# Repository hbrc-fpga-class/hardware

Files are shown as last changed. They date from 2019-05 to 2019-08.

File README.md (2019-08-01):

# Homebrew Automation Hardware

This repository contains the designs for any physical hardware for the Homebrew Automation PCB.

# tinyfpga-raspi-romi-board
These are the KiCad design files for the PCB. It's designed as follows:

* The Romi chassis needs to have the combined power distribution board and motor controller
* The Romi PDB/MC's onboard regulator **NEEDS TO BE CONFIGURED TO 3.3V OUTPUT OR EVERYTHING WILL BREAK AND YOU WILL BE SAD**
  * This is accomplished by cutting the "VREG Select" trace with an exacto knife. 
* Male headers need to be installed into the following locations (add a picture here....)
  * PWMR / DIRR / nSLPR / GND
  * PWML / DIRL / nSLPL / GND
  * ERA / ERB / GND
  * ELA / ELB / GND
  * 3x VSW / 3x GND
* The custom board should have female headers installed which mate with the male headers on the PDB/MC board
* The raspberry pi and tinyfpga plug into the custom board

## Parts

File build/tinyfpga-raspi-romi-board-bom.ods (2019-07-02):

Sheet: tinyfpga-raspi-romi-board
17 | R11, R12, R13, R14, R15, R16, R17, R18, R19, R20, R21, R3, R4, R5, R6, R7, R8 | 268 | Resistor_THT:R_Axial_DIN0204_L3.6mm_D1.6mm_P2.54mm_Vertical
1 | F1 | MF-MSMF250/16X-2 | Fuse:Fuse_1812_4532Metric_Pad1.30x3.40mm_HandSolder
1 | C2 | 1uF | Capacitor_THT:C_Rect_L4.0mm_W2.5mm_P2.50mm
1 | C1 | 22uF | Capacitor_THT:CP_Radial_D5.0mm_P2.00mm
8 | Q1, Q2, Q3, Q4, Q5, Q6, Q7, Q8 | 2N7000 | Package_TO_SOT_THT:TO-92_Inline
10 | R1, R10, R2, R22, R23, R24, R25, R26, R27, R9 | 3.9k | Resistor_THT:R_Axial_DIN0204_L3.6mm_D1.6mm_P2.54mm_Vertical
1 | U1 | CAT24C128 | Package_SO:SOIC-8_3.9x4.9mm_P1.27mm
2 | J1, J2 | PinSocket_1x14_P2.54mm_Vertical | Connector_PinSocket_2.54mm:PinSocket_1x14_P2.54mm_Vertical
8 | D2, D3, D4, D5, D6, D7, D8, D9 | LED | LED_THT:LED_D5.0mm_Clear
1 | A1 | OKR-T_3-W12-C | custom:Murata_OKR-T-3_P73
3 | J19, J6, J8 | PinHeader_1x02_P2.54mm_Vertical | Connector_PinHeader_2.54mm:PinHeader_1x02_P2.54mm_Vertical
2 | J16, J17 | PinHeader_1x03_P2.54mm_Vertical | Connector_PinHeader_2.54mm:PinHeader_1x03_P2.54mm_Vertical
1 | J9 | PinHeader_1x06_P2.54mm_Vertical | Connector_PinHeader_2.54mm:PinHeader_1x06_P2.54mm_Vertical
1 | J20 | PinHeader_2x05_P2.54mm_Vertical | Connector_PinHeader_2.54mm:PinHeader_2x05_P2.54mm_Vertical
1 | J7 | PinHeader_2x08_P2.54mm_Vertical | Connector_PinHeader_2.54mm:PinHeader_2x08_P2.54mm_Vertical
2 | J10, J11 | PinSocket_1x03_P2.54mm_Vertical | Connector_PinSocket_2.54mm:PinSocket_1x03_P2.54mm_Vertical
2 | J14, J15 | PinSocket_1x04_P2.54mm_Vertical | Connector_PinSocket_2.54mm:PinSocket_1x04_P2.54mm_Vertical
2 | J12, J13 | PinSocket_2x02_P2.54mm_Vertical | Connector_PinSocket_2.54mm:PinSocket_2x02_P2.54mm_Vertical
1 | J5 | PinSocket_2x03_P2.54mm_Vertical | Connector_PinSocket_2.54mm:PinSocket_2x03_P2.54mm_Vertical
1 | J4 | PinSocket_2x08_P2.54mm_Vertical | Connector_PinSocket_2.54mm:PinSocket_2x08_P2.54mm_Vertical
1 | J3 | PinSocket_2x20_P2.54mm_Horizontal | Connector_PinSocket_2.54mm:PinSocket_2x20_P2.54mm_Horizontal
1 | D1 | SMBJ5.0A | Diode_SMD:D_SMB_Handsoldering
3 | SW2, SW3, SW4 | SW_Push | Button_Switch_THT:SW_PUSH_6mm_H5mm

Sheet: tinyfpga
1 | https://www.digikey.com/product-detail/en/sullins-connector-solutions/GEC03DABN-M30/S2331E-03-ND/1242106
2 | https://www.digikey.com/product-detail/en/sullins-connector-solutions/PEC14SFAN/S1212E-14-ND/859455

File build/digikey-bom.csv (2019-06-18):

Index | Quantity | Part Number | Manufacturer Part Number | Description | Customer Reference | Available | Backorder | Unit Price | Extended Price USD
1 | 25 | 811-2115-5-ND | OKR-T/3-W12-C | DC DC CONVERTER 0.59-6V 15W |  | 25 | 0 | 6.01000 | 150.25
2 | 25 | 732-8938-1-ND | 860020572004 | CAP ALUM 22UF 20% 35V RADIAL |  | 25 | 0 | 0.11000 | 2.75
3 | 25 | 445-173261-1-ND | FG18X7R1E105KRT06 | CAP CER 1UF 25V X7R RADIAL |  | 25 | 0 | 0.23700 | 5.93
4 | 25 | SMBJ5.0ALFCT-ND | SMBJ5.0A | TVS DIODE 5V 9.2V DO214AA |  | 25 | 0 | 0.27560 | 6.89
5 | 200 | C5SMF-RJF-CT0W0BB2CT-ND | C5SMF-RJF-CT0W0BB2 | LED RED CLEAR 5MM OVAL T/H |  | 200 | 0 | 0.12160 | 24.32
6 | 25 | MF-MSMF250/16X-2CT-ND | MF-MSMF250/16X-2 | PTC RESET FUSE 16V 2.5A 1812 |  | 25 | 0 | 0.71900 | 17.98
7 | 200 | 2N7000FS-ND | 2N7000 | MOSFET N-CH 60V 200MA TO-92 |  | 200 | 0 | 0.24990 | 49.98
8 | 250 | BC4555CT-ND | MRS16000C3901FCT00 | RES 3.9K OHM 1% 0.4W AXIAL |  | 250 | 0 | 0.05916 | 14.79
9 | 500 | BC4552CT-ND | MRS16000C2700FCT00 | RES 270 OHM 1% 0.4W AXIAL |  | 500 | 0 | 0.04662 | 23.31
10 | 25 | CAT24C128WI-GT3CT-ND | CAT24C128WI-GT3 | IC EEPROM 128K I2C 1MHZ 8SOIC |  | 25 | 0 | 0.30900 | 7.73
11 | 75 | 450-1650-ND | 1825910-6 | SWITCH TACTILE SPST-NO 0.05A 24V |  | 75 | 0 | 0.09400 | 7.05
12 | 25 | S5534-ND | PPTC202LJBN-RC | CONN HDR 40POS 0.1 TIN PCB R/A |  | 25 | 0 | 2.32600 | 58.15
13 | 50 | S7012-ND | PPTC141LFBN-RC | CONN HDR 14POS 0.1 TIN PCB |  | 50 | 0 | 0.80300 | 40.15
14 | 25 | S1012EC-30-ND | PREC030SAAN-RC | CONN HEADER VERT 30POS 2.54MM |  | 0 | 25 | 0.48120 | 12.03
15 | 50 | S7002-ND | PPTC041LFBN-RC | CONN HDR 4POS 0.1 TIN PCB |  | 50 | 0 | 0.42400 | 21.20
16 | 50 | S7036-ND | PPPC031LFBN-RC | CONN HDR 3POS 0.1 GOLD PCB |  | 50 | 0 | 0.35100 | 17.55
17 | 50 | S7070-ND | PPTC022LFBN-RC | CONN HDR 4POS 0.1 TIN PCB |  | 50 | 0 | 0.53500 | 26.75
18 | 25 | S5673-ND | NPTC032KFMS-RC | CONN HDR 6POS 0.1 TIN SMD |  | 25 | 0 | 0.84200 | 21.05
19 | 25 | 609-5602-ND | 54202-G08-03 | CONN HEADER SMD 6POS 2.54MM |  | 25 | 0 | 0.34200 | 8.55
20 | 25 | 609-4723-ND | 54202-G0805LF | CONN HEADER SMD 10POS 2.54MM |  | 25 | 0 | 0.67300 | 16.83
21 | 25 | 609-4723-ND | 54202-G0805LF | CONN HEADER SMD 10POS 2.54MM |  | 25 | 0 | 0.67300 | 16.83
22 | 25 | S5678-ND | NPTC082KFMS-RC | CONN HDR 16POS 0.1 TIN SMD |  | 25 | 0 | 1.71100 | 42.78
23 | 6 | S1033E-06-ND | GBC06SABN-M30 | CONN HEADER SMD 6POS 2.54MM |  | 6 | 0 | 0.84000 | 5.04

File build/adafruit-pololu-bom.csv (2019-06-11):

Qty. | Item Name | URL | Unit Price | Extended Price | Notes
1 | Raspberry Pi 3 Model B+ | https://www.adafruit.com/product/3775 | $35.00 | $35.00
1 | 8 GB SDHC MicroSD Card | https://www.adafruit.com/product/1294 | $9.95 | $9.95 | Could probably get by with 4GB card if available
2 | Alkaline AA batteries (LR6) - 3 pack | https://www.adafruit.com/product/3521 | $2.25 | $4.50 | Six batteries needed per base
1 | Male/Male Jumper Wires – 20 x 3" (75mm) | https://www.adafruit.com/product/1956 | $1.95 | $1.95 | Not all 20 are needed but they’re handy to keep around
1 | TinyFPGA BX | https://www.adafruit.com/product/4038 | $38.95 | $38.95
2 | HC-SR04 Ultrasonic Sonar Distance Sensor | https://www.adafruit.com/product/3942 | $3.95 | $7.90 | Wayne can likely supply these. Should they be sourced anyway just in case?
1 | Romi Chassis Kit - Blue | https://www.pololu.com/product/3506 | $29.95 | $29.95 | Color isn’t important. Substitute others at your own discretion
1 | Romi Encoder Pair Kit, 12 CPR, 3.5-18V | https://www.pololu.com/product/3542 | $8.95 | $8.95
1 | Motor Driver and Power Distribution Board for Romi Chassis | https://www.pololu.com/product/3543 | $19.95 | $19.95
2 | QTR-MD-01RC Reflectance Sensor | https://www.pololu.com/product/4141 | $1.61 | $3.22
 |  |  | Total: | $160.32

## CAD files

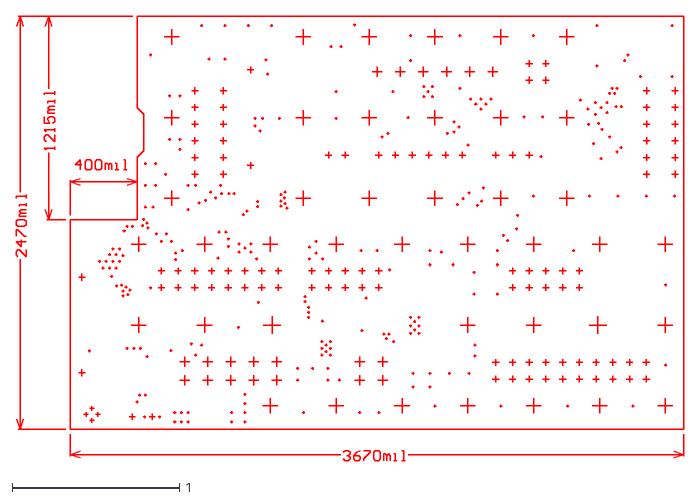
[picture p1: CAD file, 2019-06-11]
research/mech/rom02a-drill.dxf
3.99 x 2.66

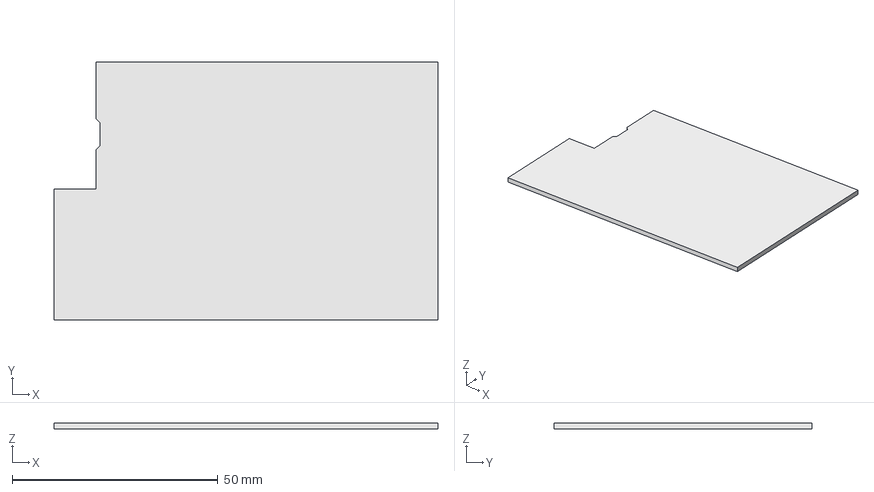
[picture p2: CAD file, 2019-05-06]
research/mech/pololu-motor-power-board.FCStd
93.2 x 62.7 x 1.57 mm

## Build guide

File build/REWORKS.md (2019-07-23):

# Homebrew Automation Board Rev A Reworks

* U1 silk is hard to understand. Doesn't _clearly_ indicate pin 1 / orientation.
* U1 address pins should probably get some thermal relief to make soldering easier
* I don't like the copper neck under F1. Looks like it could cause a short.
* While pin 1 is defined on board silk for A1, the A1 module doesn't indicate pin 1 very obviously or at all.
* I don't like the closeness of the pads for A1. Makes soldering pretty tricky when trying to avoid shorts.
* Silk on 3.3V power select is switched.
* Transistor pitch is very difficult to solder. To be honest, SOT23 would probably be easier
* Pull-downs on PWM signals are missing
* TX and RX is switched
* The male 1x14 pins I bought are too long and needed to be trimmed.
* ~Pull-down needed on romi shutdown pin~ Cut trace on shutdown pin to disable feature
* Real-time clock for Raspberry Pi
* EEPROM should always be powered from Raspberry Pi 3.3V
* In order to prevent undervolting the Pi, consider changing the 5V regulator's TRIM resistor to 255 ohm (1%)
* Add more bulk capacitance to prevent high internal resistance of Alkaline batteries from allowing VBAT

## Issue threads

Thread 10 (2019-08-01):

Silkscreen labels wrong for 3.3V power selection

swedishhat, 2019-08-01:
silk labels are switched for the headers that select the source of the 3.3V

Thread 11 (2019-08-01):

Wheels immediately start spinning when bot is turned on

swedishhat, 2019-08-01:
Workaround: externally solder on pull-down resistors on PWML and PWMR pins
Possible Enhancement: Add pull-down resistors to rev-B design

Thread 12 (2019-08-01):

MOSI and MISO SPI pin configuration for FPGA does not allow flash to be programmed

swedishhat, 2019-08-01:
As a SPI slave, the FPGAs internal SRAM can be programmed, but not the flash IC. If the MOSI/MISO lines are swapped, the

Workaround: if persistent programming is needed, connect Pi to FPGA using USB cable and use TinyProg tool

Possible enhancement: provide jumpers or programmable "switcheroo" circuit on Rev B to program either flash IC or FPGA

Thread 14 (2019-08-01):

ROMI_SHDN always asserted by Pi at boot, which immediately shuts down Pi

swedishhat, 2019-08-01:
Schematic issue because Rev A design can't be solved in SW with device tree.

Workaround: Cut trace with sharp blade to disable feature

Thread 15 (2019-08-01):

Add RTC to keep track of time between reboots

swedishhat, 2019-08-01:
Time gets reset to midnight 1/1/1970 every time the Pi is reset and NTP isn't always available to update the time to a real value. Having a reliable clock would keep the time accurate

bblodget, 2019-09-07:
An RTC would also help with timestamping ROS messages.  We should investigate if the FPGA and Pi can share access to the RTC, so they would be in sync and both could do timestamps.

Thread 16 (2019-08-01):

Move Pi's device tree EEPROM power from global 3.3v to the Pi's internal regulator

swedishhat, 2019-08-01:
Currently 3.3V is provided by the Romi so if there are issues with the 3.3V supply, the Pi may boot but the device tree EEPROM will not be powered, preventing it from setting the configuration

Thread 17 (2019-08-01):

Pi sometime undervolts with 268 ohm TRIM resistor on 5V regulator

swedishhat, 2019-08-01:
Workaround: swap out the 5V regulator's TRIM resistor to 255 ohm (1%)

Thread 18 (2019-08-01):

Add more bulk capacitance to power rails

swedishhat, 2019-08-01:
Stabilize the input voltages with more capacitors

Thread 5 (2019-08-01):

U1 silk is hard to understand

swedishhat, 2019-08-01:
Silk on U1 doesn't clearly indicate pin 1 or orientation

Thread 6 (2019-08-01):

No thermal relief for surface mount parts

swedishhat, 2019-08-01:
Issue: Thermal relief is enabled for through-hole parts but not for SMD parts. In particular, U1's GND and address pins are difficult to solder.

Possible workaround: Use a hotplate, oven, or hot air reflow station for surface-mount parts

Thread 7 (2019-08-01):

Copper necks exist between some copper pours

swedishhat, 2019-08-01:
These necks are mainly just un-aesthetic, but they provide a small sliver of copper that could facilitate an unwanted short during rework or if the soldermask is scratched off

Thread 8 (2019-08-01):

5V regulator (A1) does not indicate pin 1 on actual module

swedishhat, 2019-08-01:
Pin 1 is marked on the silkscreen of the Kicad part, but the module itself doesn't indicate pin 1.

swedishhat, 2019-08-01:
Workaround: check the module datasheet during population of the part.

Possible fix: modify the part's silkscreen to include more detail about the physical module (e.g. inductor direction)

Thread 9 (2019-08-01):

Pads too close together on tansistors and regulator

swedishhat, 2019-08-01:
The transistor population and 5v regulator population are challenging because the pin pads are very close together with no soldermask between them. These two part types are a very high risk for accidental shorts and require a keen eye during the build

swedishhat, 2019-08-01:
Workaround: Be careful during population and check continuity

Possible enhancement: Move to standard surface-mount footprints
Possible enhancement: Use triangular pad spacing footprint for transistors, adjust regulator footprint to have soldermask between pins

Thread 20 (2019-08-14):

Add I2C pin header to facilitate addition of other sensors

swedishhat, 2019-08-14:
I2C pins on the Pi are difficult to get to for adding additional sensors. Adding a pin header for these signals (and potentially others) would make prototyping with new devices and modules more accessible.

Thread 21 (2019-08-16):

Switch to QTRXL-HD Reflectance Sensors

bblodget, 2019-08-16:
We should switch to the QTRXL-HD-01RC reflectance sensor.  This is Pololu Item #4501.  It has much better range and works better as cliff sensors.  The footprint probably needs to be modified if we wish to directly connect the sensor without flying leads.

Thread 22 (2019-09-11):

battery voltage, current measurement

bblodget, 2019-09-11:
It would be nice to be able to read that battery voltage and current.  Could be done from Pi or FPGA.  It could be an interesting peripheral for the FPGA.  For example, it could be configured to generate an interrupt if the voltage goes below a certain value.  There could be a process on the Pi that would monitor that interrupt via a select loop.

swedishhat, 2019-09-11:
I like this idea. Are we still thinking alkaline batteries for the next rev or should we look into some kind of lithium pack?

bblodget, 2019-09-11:
I think we should look into a lithium pack.  Kyle had some ideas we should check with him when he gets back.

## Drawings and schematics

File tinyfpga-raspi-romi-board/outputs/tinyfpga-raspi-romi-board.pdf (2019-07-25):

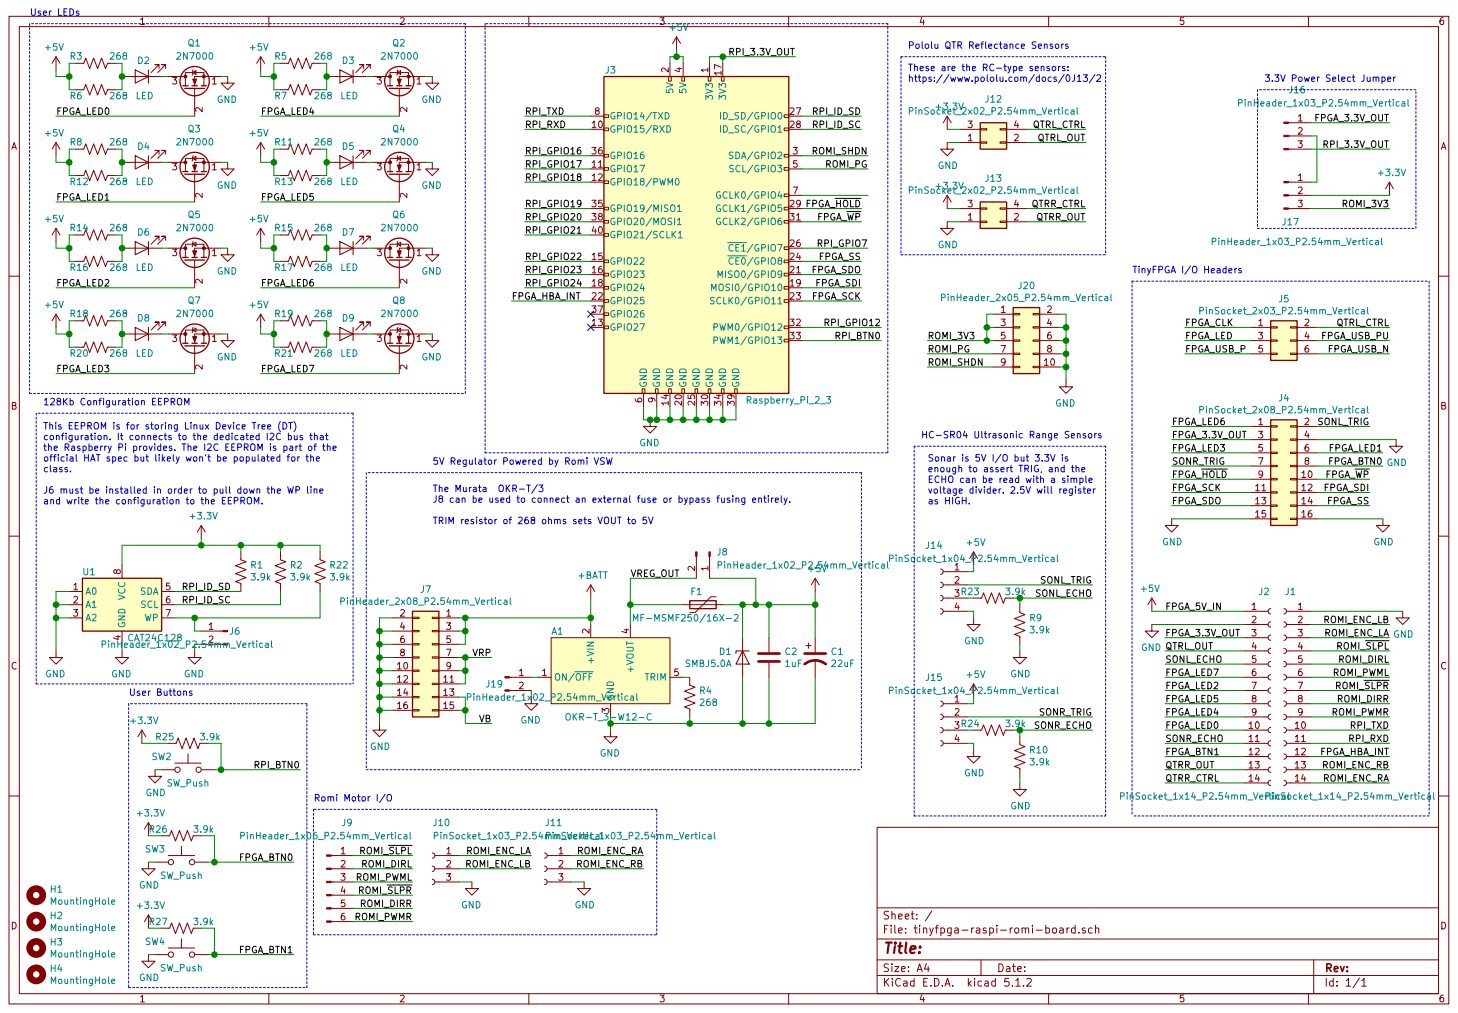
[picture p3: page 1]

https://www.pololu.com/docs/0J13/2 Pololu QTR Reflectance Sensors HC-SR04 Ultrasonic Range Sensors Sonar is 5V I/O but 3.3V is enough to assert TRIG, and the

These are the RC-type sensors:

128Kb Configuration EEPROM
voltage divider. 2.5V will register as HIGH. This EEPROM is for storing Linux Device Tree (DT)
configuration. It connects to the dedicated I2C bus that
the Raspberry Pi provides. The I2C EEPROM is part of the
official HAT spec but likely won't be populated for the
class. J6 must be installed in order to pull down the WP line

J8PinHeader_1x02_P2.54mm_Vertical The Murata OKR-T/3 J8 can be used to connect an external fuse or bypass fusing entirely. TRIM resistor of 268 ohms sets VOUT to 5V

ECHO can be read with a simple

4 SDA 5 SCL 6 WP 7 VCC

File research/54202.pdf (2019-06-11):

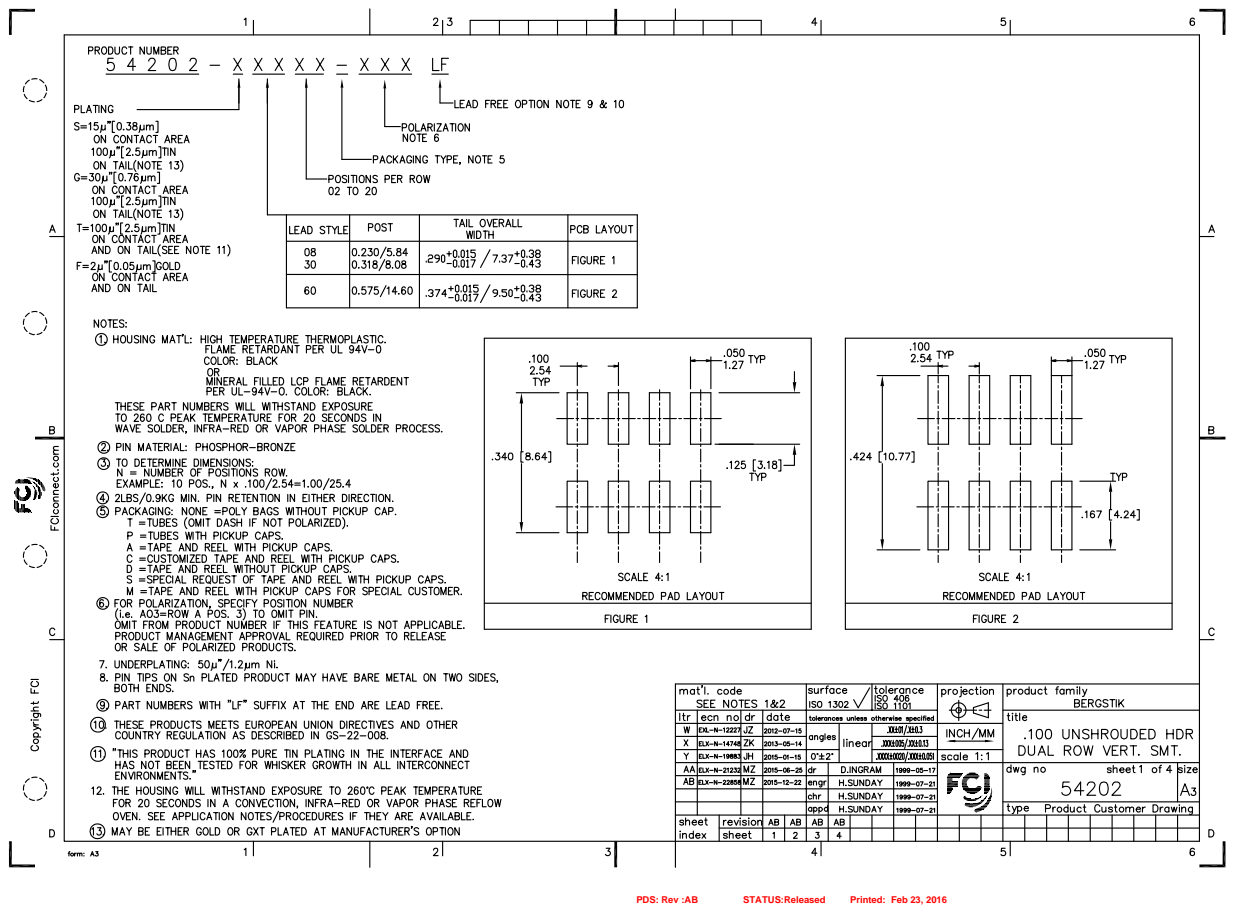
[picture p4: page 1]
PDS: Rev :AB; STATUS:Released; Printed: Feb 23, 2016

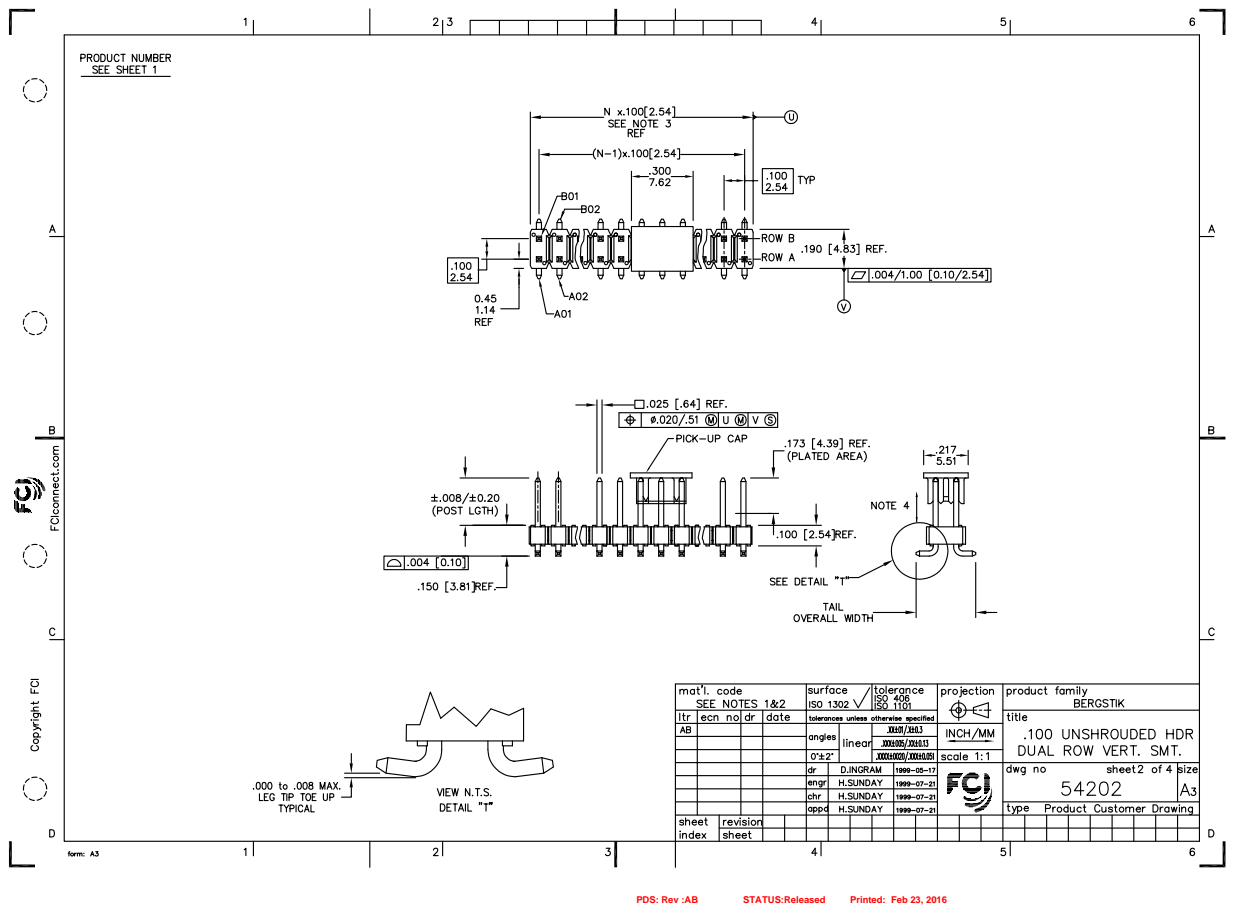
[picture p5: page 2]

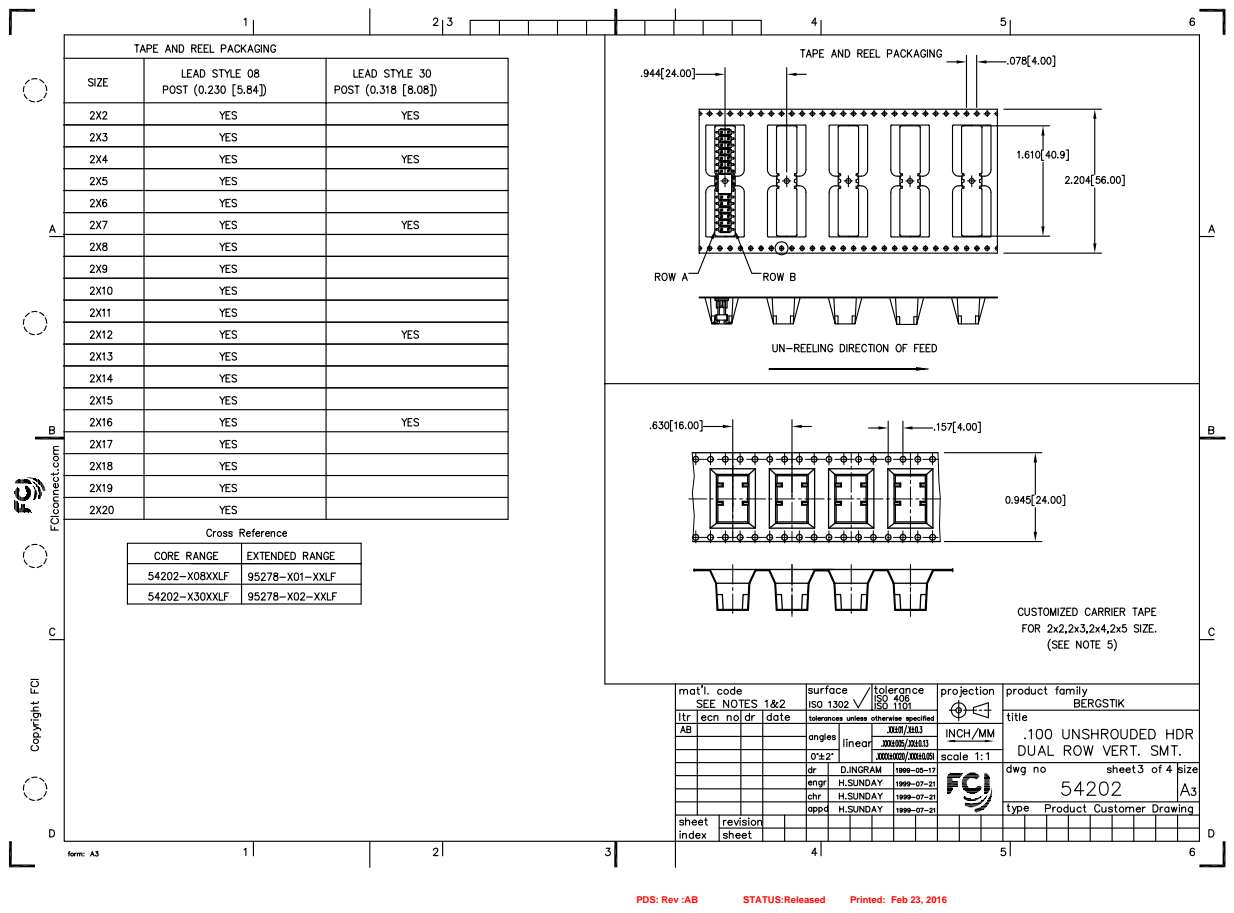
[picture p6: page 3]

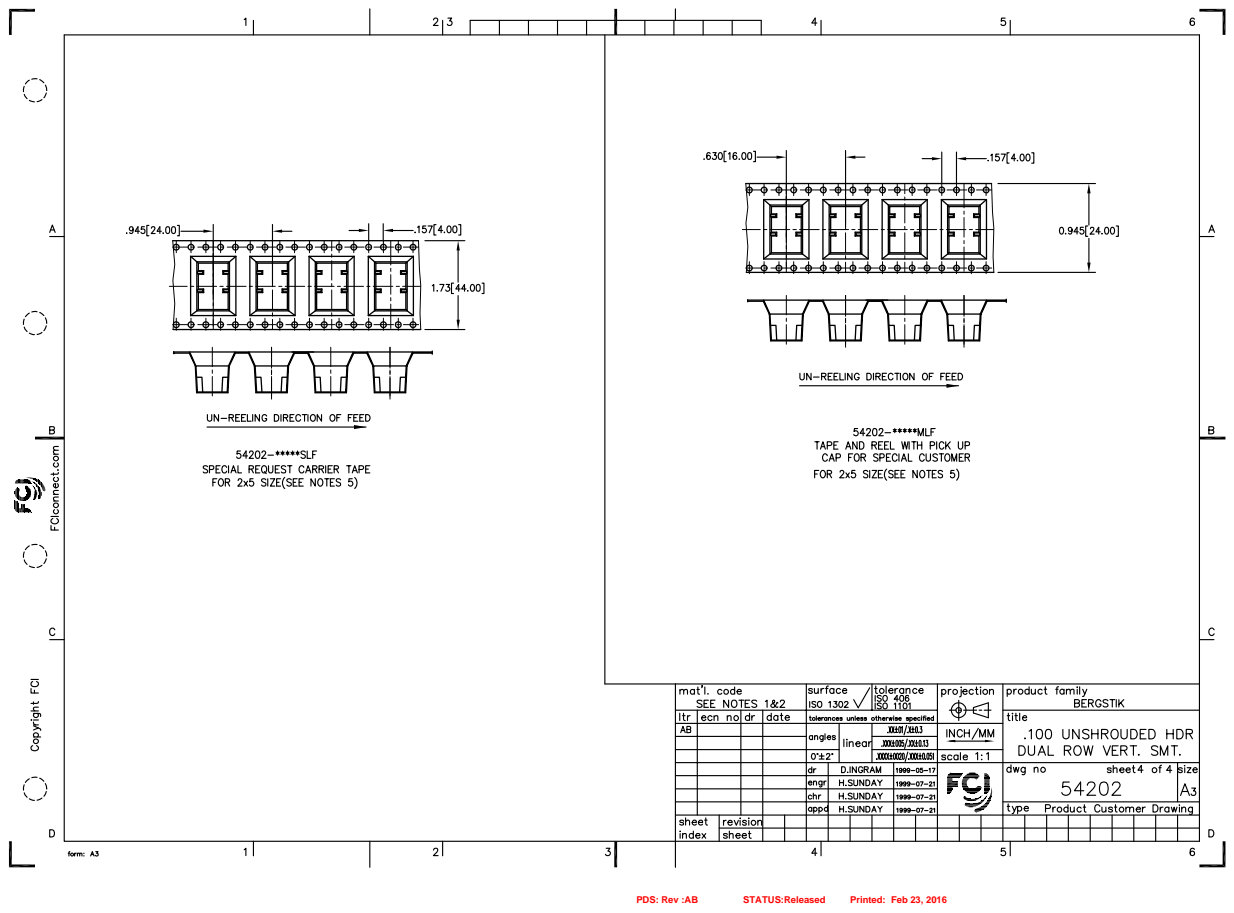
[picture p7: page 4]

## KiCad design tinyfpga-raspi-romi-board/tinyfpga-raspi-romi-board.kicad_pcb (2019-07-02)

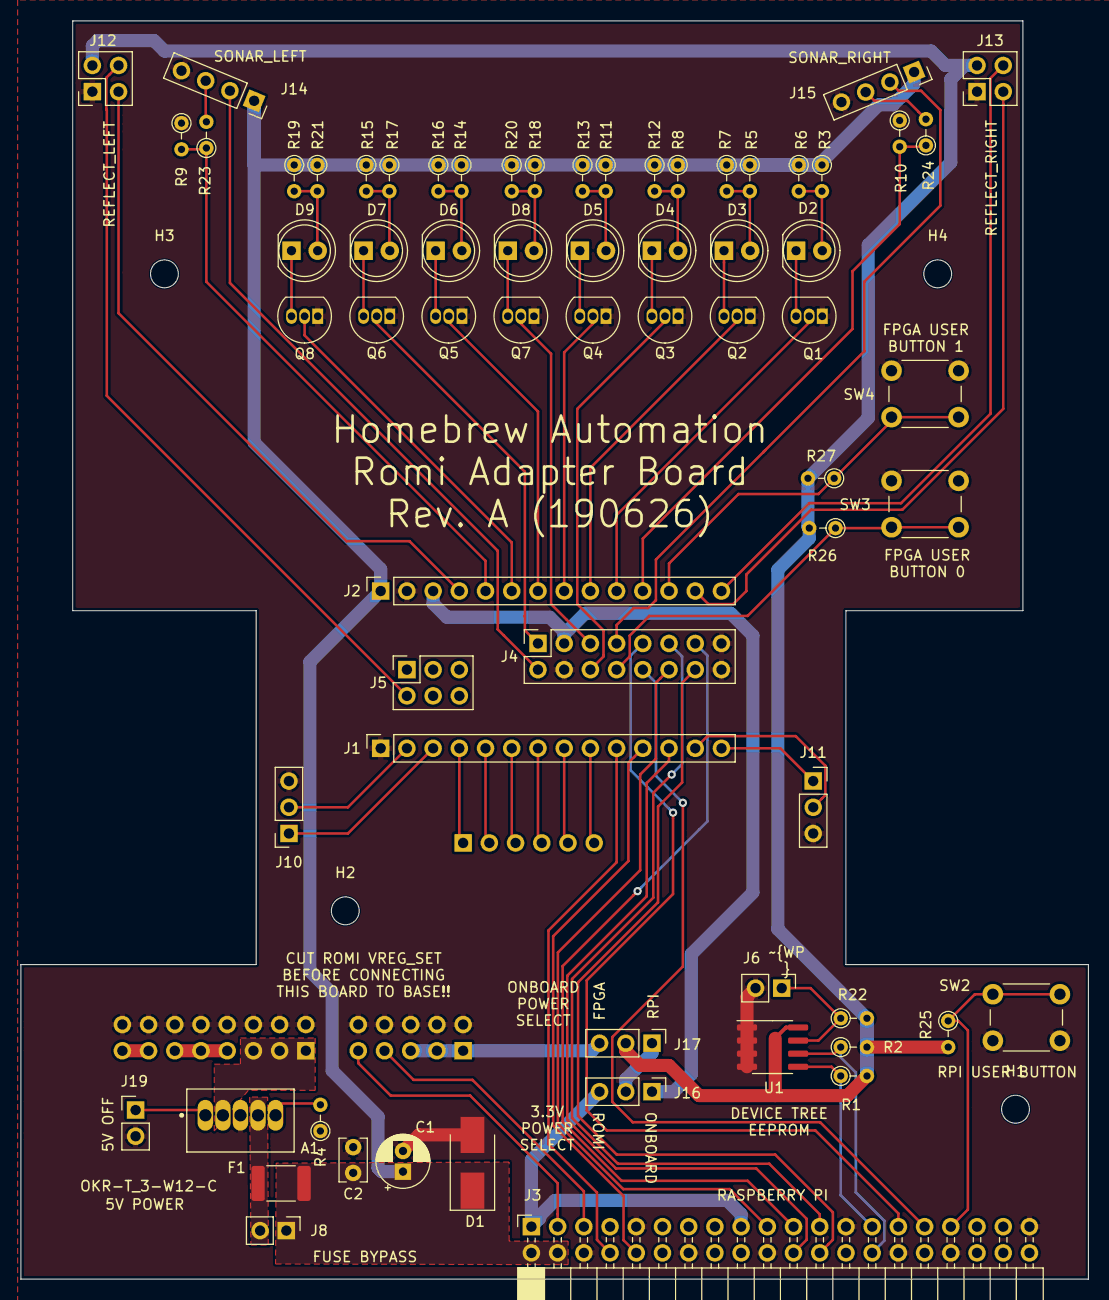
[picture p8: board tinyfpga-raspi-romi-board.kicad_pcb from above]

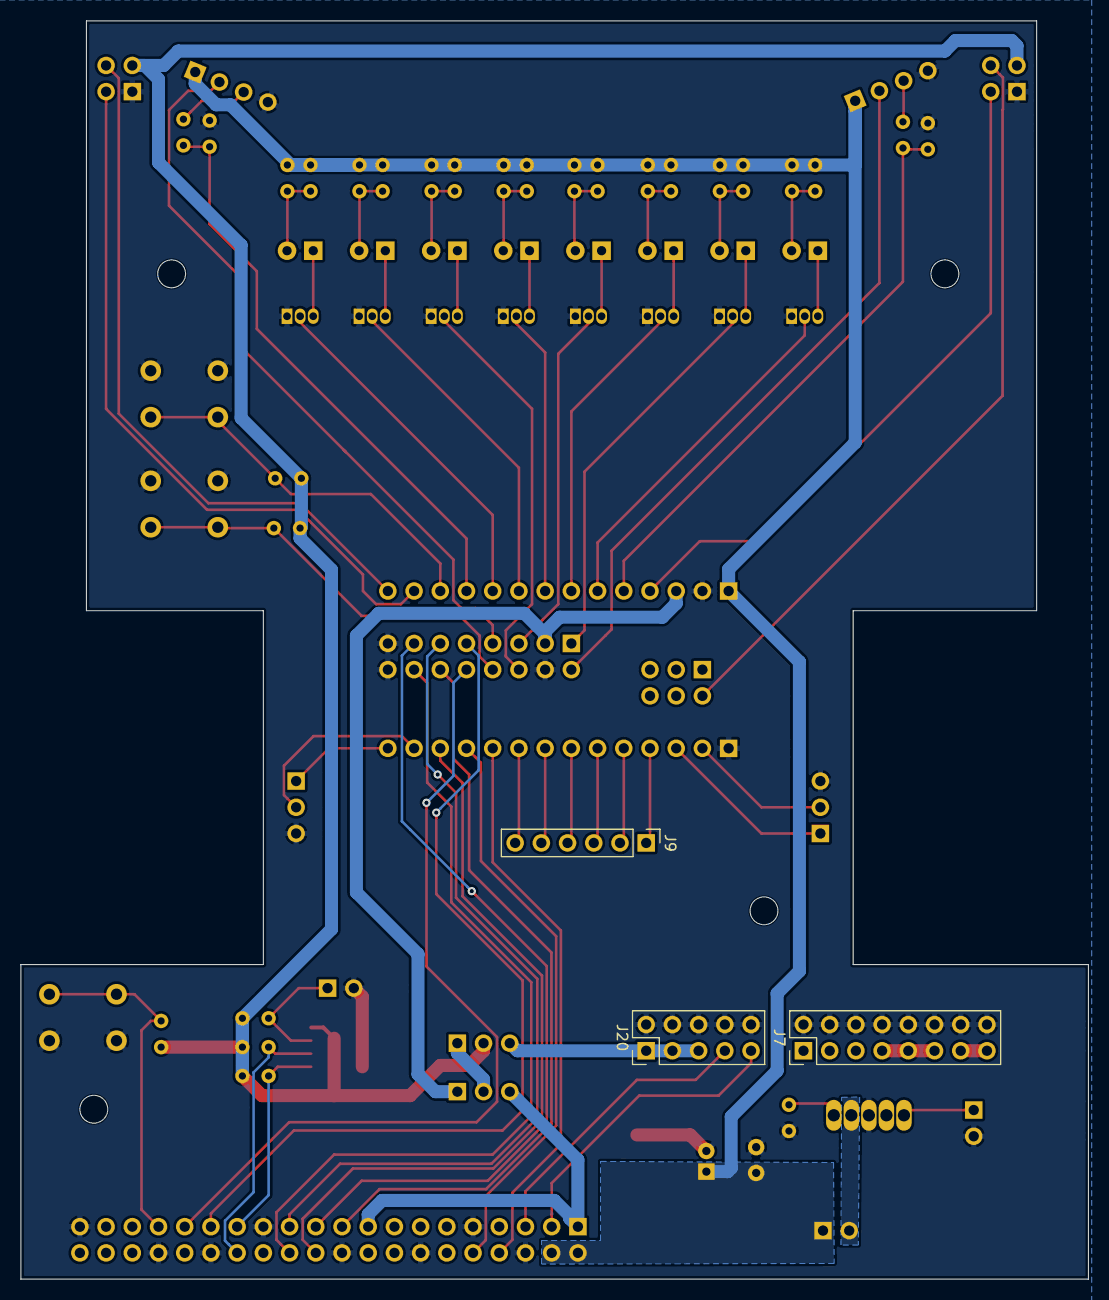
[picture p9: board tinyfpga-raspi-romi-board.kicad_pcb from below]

Board: 2 copper layers, 103.4 x 121.9 mm, 75 parts (3 on the bottom side), 74 nets.

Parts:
A1: OKR-T_3-W12-C; Murata_OKR-T-3_P73
C1: 22uF; CP_Radial_D5.0mm_P2.00mm
C2: 1uF; C_Rect_L4.0mm_W2.5mm_P2.50mm
D1: SMBJ5.0A; D_SMB_Handsoldering
D2, D3, D4, D5, D6, D7, D8, D9: LED; LED_D5.0mm_Clear
F1: MF-MSMF250/16X-2; Fuse_1812_4532Metric_Pad1.30x3.40mm_HandSolder
H1, H2, H3, H4: MountingHole; MountingHole_2.7mm_M2.5
J1, J2: Conn_01x14_Female; PinSocket_1x14_P2.54mm_Vertical
J3: Raspberry_Pi_2_3; PinSocket_2x20_P2.54mm_Horizontal
J4: PinSocket_2x08_P2.54mm_Vertical
J5: PinSocket_2x03_P2.54mm_Vertical
J6, J8: PinHeader_1x02_P2.54mm_Vertical
J7: PinHeader_2x08_P2.54mm_Vertical
J9: PinHeader_1x06_P2.54mm_Vertical
J10, J11: PinSocket_1x03_P2.54mm_Vertical
J12, J13: PinSocket_2x02_P2.54mm_Vertical
J14, J15: PinSocket_1x04_P2.54mm_Vertical
J16, J17: PinHeader_1x03_P2.54mm_Vertical
J19: ON_OFF; PinHeader_1x02_P2.54mm_Vertical
J20: PinHeader_2x05_P2.54mm_Vertical
Q1, Q2, Q3, Q4, Q5, Q6, Q7, Q8: 2N7000; TO-92_Inline
R1, R2, R9, R10, R22, R23, R24, R25, R26, R27: 3.9k; R_Axial_DIN0204_L3.6mm_D1.6mm_P2.54mm_Vertical
R3, R4, R5, R6, R7, R8, R11, R12, R13, R14, R15, R16, R17, R18, R19, R20, R21: 268; R_Axial_DIN0204_L3.6mm_D1.6mm_P2.54mm_Vertical
SW2, SW3, SW4: SW_Push; SW_PUSH_6mm_H5mm
U1: CAT24C128; SOIC-8_3.9x4.9mm_P1.27mm

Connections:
+3V3: J12.3, J13.3, J17.2, R1.2, R2.2, R22.2, R25.2, R26.2, R27.2, U1.8
+5V: C1.1, C2.1, D1.1, F1.1, J2.1, J3.2, J3.4, J8.1, J14.1, J15.1, R3.1, R5.1, R6.1, R7.1, R8.1, R11.1, R12.1, R13.1, R14.1, R15.1, R16.1, R17.1, R18.1, R19.1, R20.1, R21.1
+BATT: A1.2, J7.1, J7.3, J7.5
/FPGA_3.3V_OUT: J2.3, J4.3, J16.1
/FPGA_BTN0: J4.8, R26.1, SW3.2
/FPGA_BTN1: J2.12, R27.1, SW4.2
/FPGA_HBA_INT: J1.12, J3.22
/FPGA_LED0: J2.10, Q1.2
/FPGA_LED1: J4.6, Q3.2
/FPGA_LED2: J2.7, Q5.2
/FPGA_LED3: J4.5, Q7.2
/FPGA_LED4: J2.9, Q2.2
/FPGA_LED5: J2.8, Q4.2
/FPGA_LED6: J4.1, Q6.2
/FPGA_LED7: J2.6, Q8.2
/FPGA_SCK: J3.23, J4.11
/FPGA_SDI: J3.19, J4.12
/FPGA_SDO: J3.21, J4.13
/FPGA_SS: J3.24, J4.14
/FPGA_~HOLD: J3.29, J4.9
/FPGA_~WP: J3.31, J4.10
/QTRL_CTRL: J5.2, J12.4
/QTRL_OUT: J2.4, J12.2
/QTRR_CTRL: J2.14, J13.4
/QTRR_OUT: J2.13, J13.2
/ROMI_3V3: J17.3, J20.1, J20.3, J20.5
/ROMI_DIRL: J1.5, J9.2
/ROMI_DIRR: J1.8, J9.5
/ROMI_ENC_LA: J1.3, J10.1
/ROMI_ENC_LB: J1.2, J10.2
/ROMI_ENC_RA: J1.14, J11.1
/ROMI_ENC_RB: J1.13, J11.2
/ROMI_PG: J3.5, J20.7
/ROMI_PWML: J1.6, J9.3
/ROMI_PWMR: J1.9, J9.6
/ROMI_SHDN: J3.3, J20.9
/ROMI_~SLPL: J1.4, J9.1
/ROMI_~SLPR: J1.7, J9.4
/RPI_3.3V_OUT: J3.1, J3.17, J16.3
/RPI_BTN0: J3.33, R25.1, SW2.2
/RPI_ID_SC: J3.28, R2.1, U1.6
/RPI_ID_SD: J3.27, R1.1, U1.5
/RPI_RXD: J1.11, J3.10
/RPI_TXD: J1.10, J3.8
/SONL_ECHO: J2.5, R9.2, R23.1
/SONL_TRIG: J4.2, J14.2
/SONR_ECHO: J2.11, R10.2, R24.1
/SONR_TRIG: J4.7, J15.2
/VB: J7.13, J7.15
/VREG_OUT: A1.4, F1.2, J8.2
/VRP: J7.7, J7.9, J7.11
GND: A1.3, C1.2, C2.2, D1.2, J1.1, J2.2, J3.6, J3.9, J3.14, J3.20, J3.25, J3.30, J3.34, J3.39, J4.4, J4.15, J4.16, J6.2, J7.2, J7.4, J7.6, J7.8, J7.10, J7.12, J7.14, J7.16, J10.3, J11.3, J12.1, J13.1, J14.4, J15.4, J19.2, J20.2, J20.4, J20.6, J20.8, J20.10, Q1.1, Q2.1, Q3.1, Q4.1, Q5.1, Q6.1, Q7.1, Q8.1, R4.1, R9.1, R10.1, SW2.1, SW3.1, SW4.1, U1.1, U1.2, U1.3, U1.4
unnamed: A1.1, J19.1
unnamed: A1.5, R4.2
unnamed: D2.1, Q1.3
unnamed: D2.2, R3.2, R6.2
unnamed: D3.1, Q2.3
unnamed: D3.2, R5.2, R7.2
unnamed: D4.1, Q3.3
unnamed: D4.2, R8.2, R12.2
unnamed: D5.1, Q4.3
unnamed: D5.2, R11.2, R13.2
unnamed: D6.1, Q5.3
unnamed: D6.2, R14.2, R16.2
unnamed: D7.1, Q6.3
unnamed: D7.2, R15.2, R17.2
unnamed: D8.1, Q7.3
unnamed: D8.2, R18.2, R20.2
unnamed: D9.1, Q8.3
unnamed: D9.2, R19.2, R21.2
unnamed: J6.1, R22.1, U1.7
unnamed: J14.3, R23.2
unnamed: J15.3, R24.2
unnamed: J16.2, J17.1

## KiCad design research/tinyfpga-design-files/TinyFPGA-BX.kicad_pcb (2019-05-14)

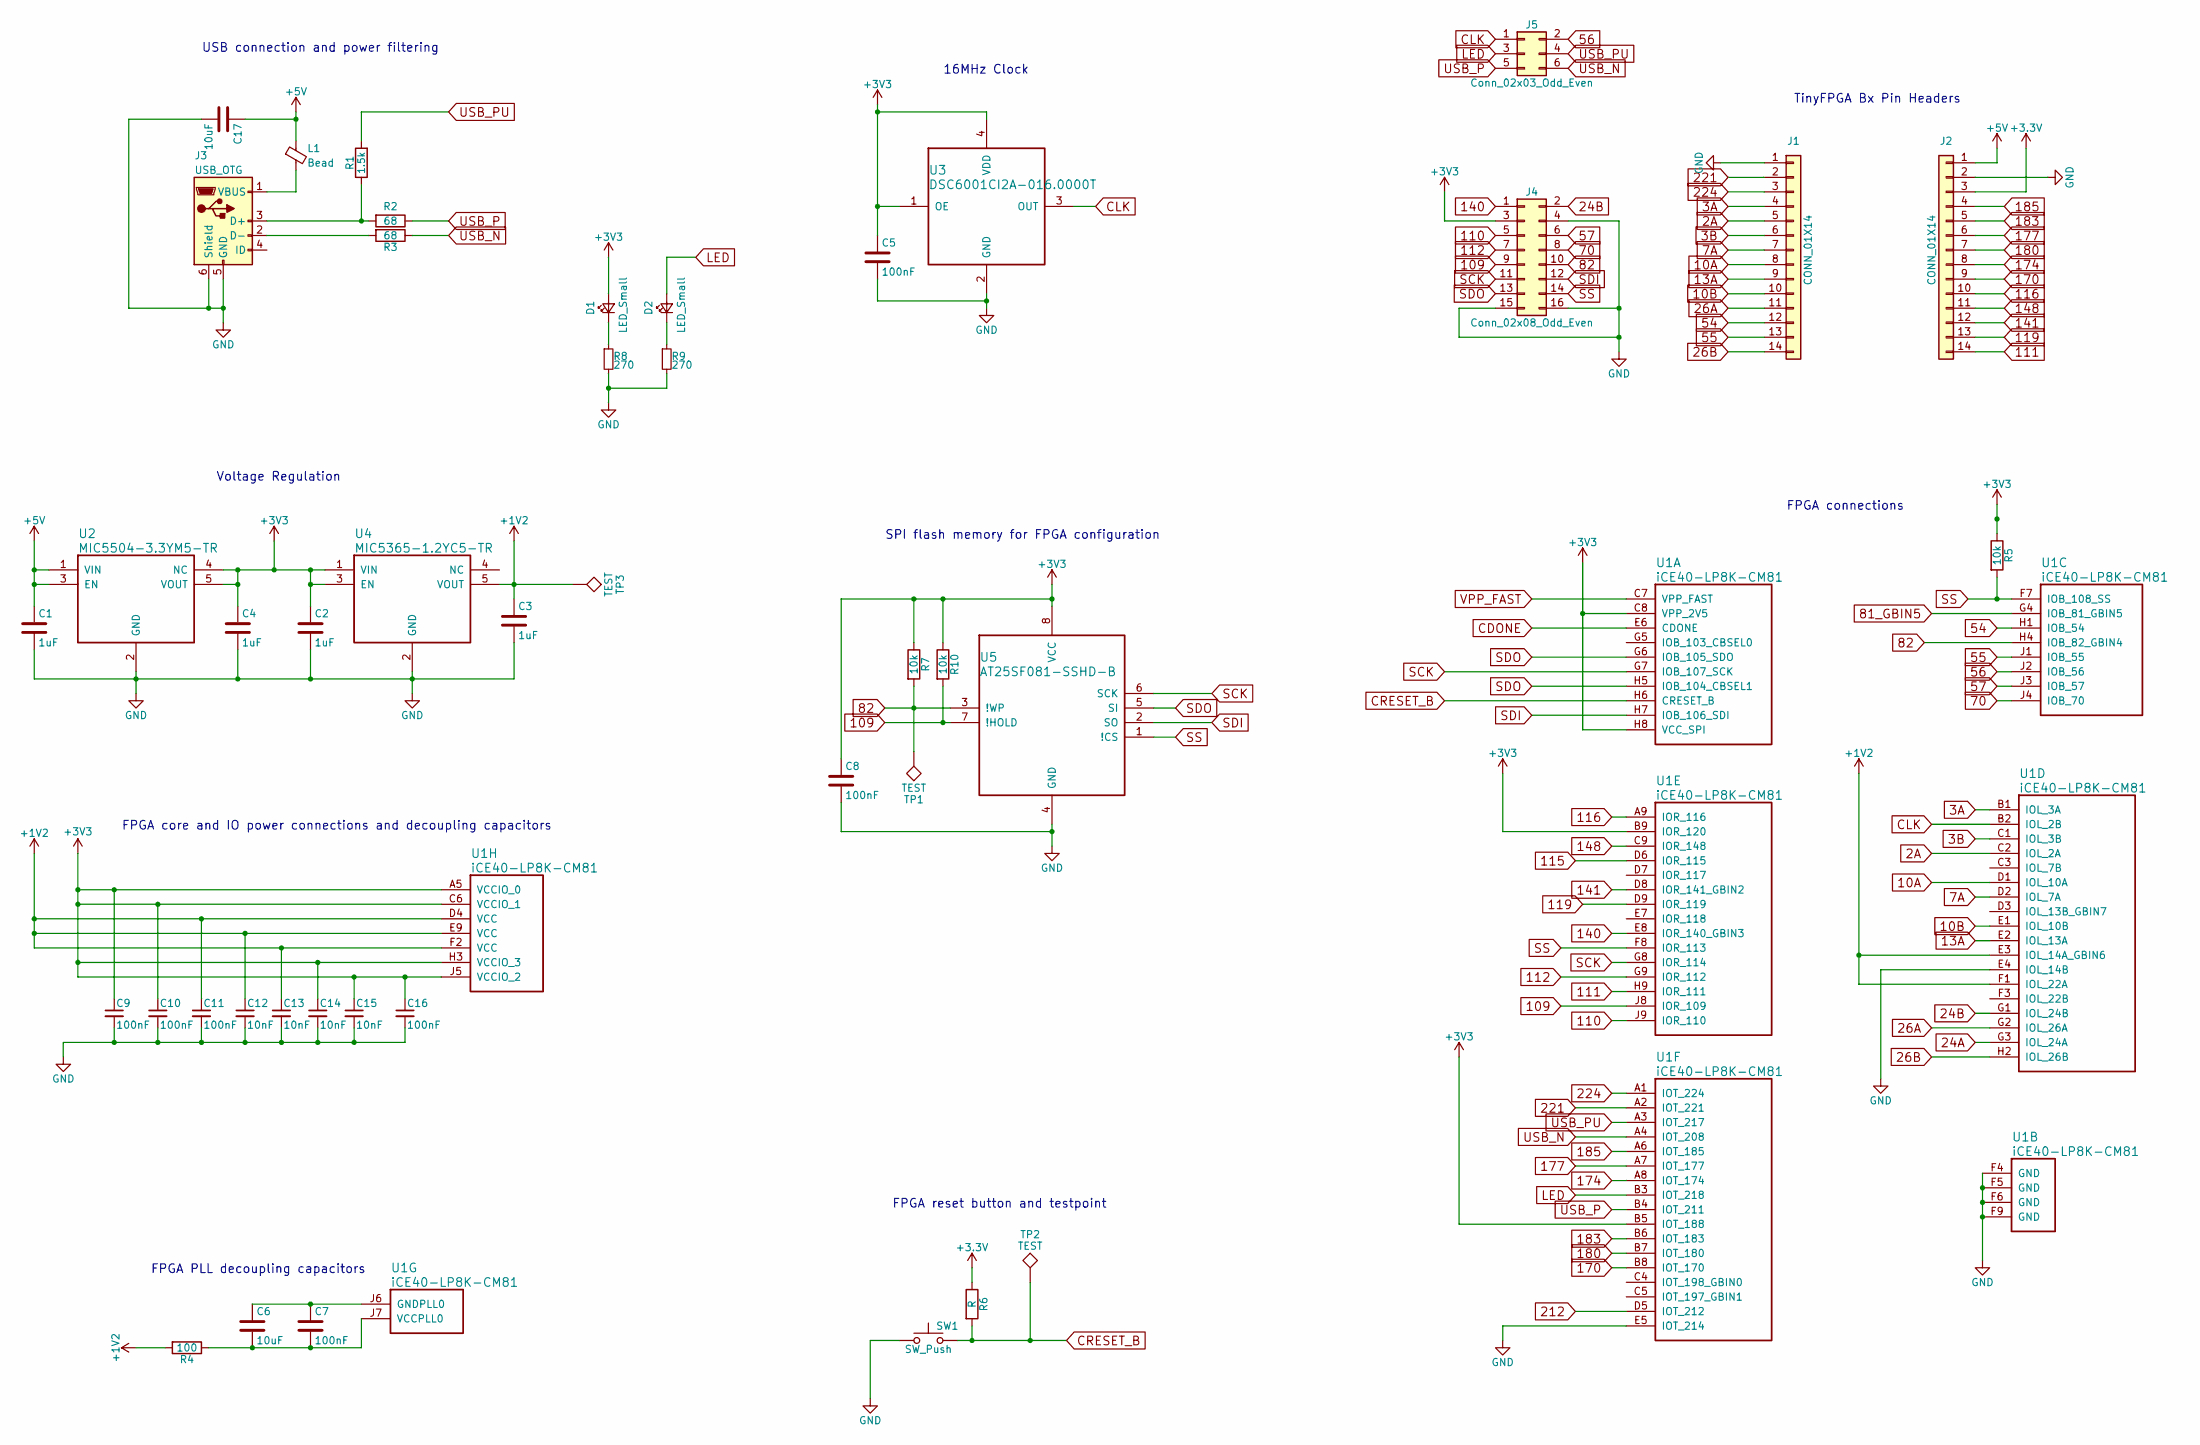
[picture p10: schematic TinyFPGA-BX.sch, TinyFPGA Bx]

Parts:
C1, C2, C3, C4: 1uF; C_0402_NoSilk
C5, C7, C8, C9, C10, C11, C16: 100nF; C_0402_NoSilk
C6, C17: 10uF; C_0603
C12, C13, C14, C15: 10nF; C_0402_NoSilk
D1, D2: LED_Small; LED_0603
J1, J2: CONN_01X14; Pin_Header_Straight_1x14_Pitch2.54mm
J3: USB_OTG; USB_Micro-B
J4: Conn_02x08_Odd_Even; Pin_Header_Straight_2x08_Pitch2.54mm_SMD
J5: Conn_02x03_Odd_Even; Pin_Header_Straight_2x03_Pitch2.54mm_SMD
L1: Bead; L_0603
R1: 1.5k; R_0402_NoSilk
R2, R3: 68; R_0402_NoSilk
R4: 100; R_0402_NoSilk
R5, R7, R10: 10k; R_0402_NoSilk
R6: R; R_0402
R8, R9: 270; R_0402_NoSilk
SW1: SW_Push; PTS_810_SMT_Switch
TP1, TP2, TP3: TEST; Measurement_Point_Round-SMD-Pad_Small
U1: iCE40-LP8K-CM81; CM81
U2: MIC5504-3.3YM5-TR; SC-70-C5
U3: DSC6001CI2A-016.0000T; CDFN3225-4LD-PL-1
U4: MIC5365-1.2YC5-TR; SC-70-C5
U5: AT25SF081-SSHD-B; SOIC-8-1EP_3.9x4.9mm_Pitch1.27mm

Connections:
2A: J1.5, U1.C2 (IOL_2A)
3A: J1.4, U1.B1 (IOL_3A)
3B: J1.6, U1.C1 (IOL_3B)
7A: J1.7, U1.D2 (IOL_7A)
10A: J1.8, U1.D1 (IOL_10A)
10B: J1.10, U1.E1 (IOL_10B)
13A: J1.9, U1.E2 (IOL_13A)
24A: U1.G3 (IOL_24A)
24B: J4.2, U1.G1 (IOL_24B)
26A: J1.11, U1.G2 (IOL_26A)
26B: J1.14, U1.H2 (IOL_26B)
54: J1.12, U1.H1 (IOB_54)
55: J1.13, U1.J1 (IOB_55)
56: J5.2, U1.J2 (IOB_56)
57: J4.6, U1.J3 (IOB_57)
70: J4.8, U1.J4 (IOB_70)
81_GBIN5: U1.G4 (IOB_81_GBIN5)
82: J4.10, R7.2, TP1.1, U1.H4 (IOB_82_GBIN4), U5.3 (!WP)
109: J4.9, R10.2, U1.J8 (IOR_109), U5.7 (!HOLD)
110: J4.5, U1.J9 (IOR_110)
111: J2.14, U1.H9 (IOR_111)
112: J4.7, U1.G9 (IOR_112)
115: U1.D6 (IOR_115)
116: J2.10, U1.A9 (IOR_116)
119: J2.13, U1.D9 (IOR_119)
140: J4.1, U1.E8 (IOR_140_GBIN3)
141: J2.12, U1.D8 (IOR_141_GBIN2)
148: J2.11, U1.C9 (IOR_148)
170: J2.9, U1.B8 (IOT_170)
174: J2.8, U1.A8 (IOT_174)
177: J2.6, U1.A7 (IOT_177)
180: J2.7, U1.B7 (IOT_180)
183: J2.5, U1.B6 (IOT_183)
185: J2.4, U1.A6 (IOT_185)
212: U1.D5 (IOT_212)
221: J1.2, U1.A2 (IOT_221)
224: J1.3, U1.A1 (IOT_224)
+1V2: C3.1, C11.1, C12.1, C13.1, R4.2, TP3.1, U1.D4 (VCC), U1.E3 (IOL_14A_GBIN6), U1.E9 (VCC), U1.F1 (IOL_22A), U1.F2 (VCC), U4.5 (VOUT)
+5V: C1.1, C17.1, J2.1, L1.1, U2.1 (VIN), U2.3 (EN)
CDONE: U1.E6 (CDONE)
CLK: J5.1, U1.B2 (IOL_2B), U3.3 (OUT)
CRESET_B: R6.2, SW1.2, TP2.1, U1.H6 (CRESET_B)
GND: C1.2, C2.2, C3.2, C4.2, C5.2, C8.2, C9.2, C10.2, C11.2, C12.2, C13.2, C14.2, C15.2, C16.2, C17.2, J1.1, J2.2, J3.5 (GND), J3.6 (Shield), J4.4, J4.15, J4.16, R8.2, R9.2, SW1.1, U1.E4 (IOL_14B), U1.E5 (IOT_214), U1.F4 (GND), U1.F5 (GND), U1.F6 (GND), U1.F9 (GND), U2.2 (GND), U3.2 (GND), U4.2 (GND), U5.4 (GND)
LED: D2.2 (A), J5.3, U1.B3 (IOT_218)
unnamed: C6.1, C7.1, U1.J6 (GNDPLL0)
unnamed: C6.2, C7.2, R4.1, U1.J7 (VCCPLL0)
unnamed: D1.1 (K), R8.1
unnamed: D2.1 (K), R9.1
unnamed: J3.1 (VBUS), L1.2
unnamed: J3.2 (D-), R3.2
unnamed: J3.3 (D+), R1.1, R2.2
SCK: J4.11, U1.G7 (IOB_107_SCK), U1.G8 (IOR_114), U5.6 (SCK)
SDI: J4.12, U1.H7 (IOB_106_SDI), U5.2 (SO)
SDO: J4.13, U1.G6 (IOB_105_SDO), U1.H5 (IOB_104_CBSEL1), U5.5 (SI)
SS: J4.14, R5.2, U1.F7 (IOB_108_SS), U1.F8 (IOR_113), U5.1 (!CS)
USB_N: J5.6, R3.1, U1.A4 (IOT_208)
USB_P: J5.5, R2.1, U1.B4 (IOT_211)
USB_PU: J5.4, R1.2, U1.A3 (IOT_217)
VPP_FAST: U1.C7 (VPP_FAST)

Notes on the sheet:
FPGA core and IO power connections and decoupling capacitors
FPGA PLL decoupling capacitors
USB connection and power filtering
Voltage Regulation
16MHz Clock
SPI flash memory for FPGA configuration
FPGA reset button and testpoint
FPGA connections
TinyFPGA Bx Pin Headers

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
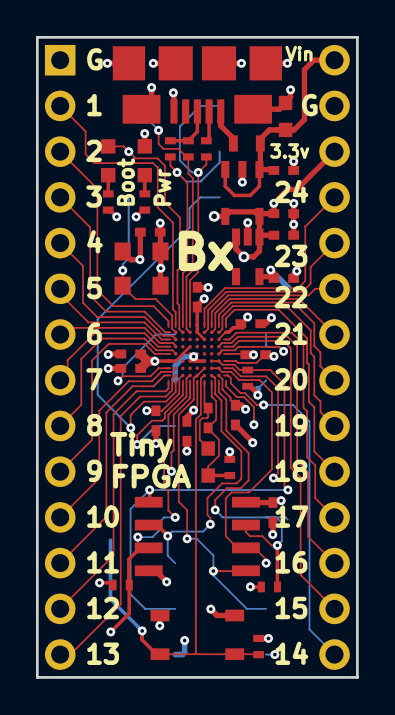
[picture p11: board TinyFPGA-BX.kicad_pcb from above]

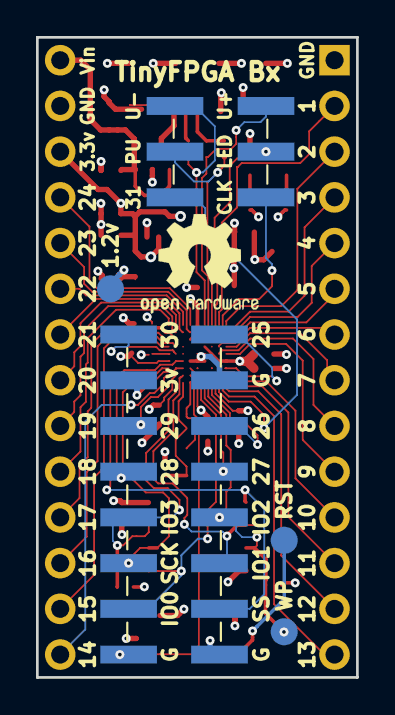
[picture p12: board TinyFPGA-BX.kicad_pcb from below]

Board: 4 copper layers, 17.8 x 35.6 mm, 44 parts (5 on the bottom side), 54 nets.

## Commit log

2019-05-06 initial commit with board files and mech
    [pololu-motor-power-board.FCStd, tinyfpga-raspi-romi-board.kicad_pcb, tinyfpga-raspi-romi-board.sch]
2019-05-13 added more to schem, notably the 5v TH reg
2019-05-14 Added all headers connnecting the custom board to the romi pdb-mc board
    [tinyfpga-raspi-romi-board.sch]
2019-05-14 annotated the parts. woah. big change
    [tinyfpga-raspi-romi-board.sch]
2019-05-14 added sensor connectors. wired more or less everything together. broke out FPGA SPI flash pins
    [tinyfpga-raspi-romi-board.sch]
2019-05-14 Added schematic for reference
2019-05-14 fixing submodule path
    [TinyFPGA-BX-2019-05-06-01-00-32.sch, TinyFPGA-BX.kicad_pcb, TinyFPGA-BX.sch]
2019-05-22 organization and labeling of hardware block
    [tinyfpga-raspi-romi-board.sch]
2019-05-30 added some formatting for pres
    [tinyfpga-raspi-romi-board.sch]
2019-06-03 contains info about supplier modules. digikey bom to come later
    [adafruit-pololu-bom.csv]
2019-06-03 reorganized hw directory
    [TinyFPGA-BX-2019-05-06-01-00-32.sch, TinyFPGA-BX.kicad_pcb, TinyFPGA-BX.sch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]
2019-06-03 added leds and user buttons. needs to be refactored to more sheets
    [tinyfpga-raspi-romi-board.sch]
2019-06-04 cluttered and gross... JUST THE WAY I LIKE IT
    [tinyfpga-raspi-romi-board.sch]
2019-06-05 finally got footprints on a board. starting arranging them
    [tinyfpga-raspi-romi-board.sch]
2019-06-05 kicad crashed but work was recovered. don't need autosave
2019-06-11 imported mech drawings to kicad pcb for placement
    [adafruit-pololu-bom.csv, rom02a-drill.dxf, tinyfpga-raspi-romi-board.kicad_pcb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]
2019-06-11 made some minor tweaks and measured tinypcb with headers
    [tinyfpga-raspi-romi-board.kicad_pcb, tinyfpga-raspi-romi-board.sch]
2019-06-13 Everything fits on a board
    [tinyfpga-raspi-romi-board.kicad_pcb, tinyfpga-raspi-romi-board.sch]
2019-06-13 All components placed on board. Needs routing doe
    [tinyfpga-raspi-romi-board.kicad_pcb, tinyfpga-raspi-romi-board.sch]
2019-06-14 Spaced out componenets more
    [tinyfpga-raspi-romi-board.kicad_pcb, tinyfpga-raspi-romi-board.sch]
2019-06-18 oh hey look its all through hole
    [digikey-bom.csv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]
2019-06-20 updated mechanical dimensions, moved power and buttons
    [tinyfpga-raspi-romi-board.kicad_pcb, tinyfpga-raspi-romi-board.sch]
2019-06-20 incorporated some of wayne and brandons adjustements
    [tinyfpga-raspi-romi-board.kicad_pcb, tinyfpga-raspi-romi-board.sch]
2019-06-20 removed the rescue files because FUCK IT THAT'S WHY
    [TinyFPGA-BX-2019-05-06-01-00-32.sch]
2019-06-24 happy with power section
    [tinyfpga-raspi-romi-board.kicad_pcb]
2019-06-24 happy with mechanicals. routing and pin swapping
    [tinyfpga-raspi-romi-board.kicad_pcb, tinyfpga-raspi-romi-board.sch]
2019-06-24 mostly done routing but have a few more rpi signals to deal with
    [tinyfpga-raspi-romi-board.kicad_pcb, tinyfpga-raspi-romi-board.sch]
2019-06-24 signals routed. needs silk and drc
    [tinyfpga-raspi-romi-board.kicad_pcb, tinyfpga-raspi-romi-board.sch]
2019-06-24 changed mount hole size and aligned them better. added pwm pulldowns
    [tinyfpga-raspi-romi-board.kicad_pcb, tinyfpga-raspi-romi-board.sch]
2019-06-26 rev-a sent to fab
    [tinyfpga-raspi-romi-board-B_Cu.gbl, tinyfpga-raspi-romi-board-B_Mask.gbs, tinyfpga-raspi-romi-board-B_Paste.gbp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]
2019-06-30 updated schematic and PDF
    [tinyfpga-raspi-romi-board.sch]
2019-07-02 cleaned up bom
    [tinyfpga-raspi-romi-board-bom.ods, tinyfpga-raspi-romi-board.csv, tinyfpga-raspi-romi-board.kicad_pcb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]
2019-07-02 moved bom into build
    [tinyfpga-raspi-romi-board-bom.ods, tinyfpga-raspi-romi-board.ods]
2019-07-22 Add couple more rework notes
2019-07-22 pulldown resistor ineffective. disabling feature instead
2019-08-01 minor readme changes
    [tinyfpga-raspi-romi-board-B_Cu.gbl, tinyfpga-raspi-romi-board-B_Mask.gbs, tinyfpga-raspi-romi-board-B_Paste.gbp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]
2019-08-01 moved outputs out of main project folder
    [tinyfpga-raspi-romi-board-B_Cu.gbl, tinyfpga-raspi-romi-board-B_Mask.gbs, tinyfpga-raspi-romi-board-B_Paste.gbp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]
